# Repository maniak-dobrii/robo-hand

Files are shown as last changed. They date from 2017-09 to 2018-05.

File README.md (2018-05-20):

## I designed this robot to show finger to my friend

You will blame me for the size of that gif

Wi-Fi enabled robot that mimics human palm. Each finger is a set of rigid segments connected via revolute joints with rubber bands pulling them together. Each finger is flexed by servo, that is attached to it via fishing line (rubber bands extend it back). Servos are controlled by ESP8266 based board.

You'll need [SketchUp](https://www.sketchup.com/) to export frame models for printing, palm is available in both `.stl` and `.skp`. [Autodesk Eagle](https://www.autodesk.com/products/eagle/free-download) is required  to export mask for PCB. Both SketchUp and Eagle have free versions enough for export.

Currently there is basic Wi-Fi-based control and two physical buttons, one for finger gesture, one for sign of the horns. Device spawns Wi-Fi hot spot and HTTP server, that serves HTML and performs gestures on GET.

### Palm
Palm itself is based on [design by Juan Gutierrez](https://www.thingiverse.com/thing:14986). In original design I didn't like thumb placement. If you only need the palm, I have it on [thingiverse](https://www.thingiverse.com/thing:2743350).

Except, of course, a 3D printer and filament, for palm you'll need:
 - **fishing line** to attach fingers to servos, could be found in a supermarket or fishing equipment store, anything will go,
 - **21 x m3x12 screws and nuts** (4 for each finger, thumb needs 3, 2 for binding palm base halfs)
 - **at least 14 1/4” rubber bands**, you might need more depending on their strength (but don't worry they are cheap and sold in big enough amounts). You can get those in orthodontic shops, they are 1/4” in diameter. In Russian they are called "эластики" or "ортодонтические резинки" or "резиновые тяги", they also have names for different hardnesses, I got "Медведь" 1/4, 4,5oz (strong), "Сова" 1/4, 2oz (weak one).

For more details see my [thingiverse](https://www.thingiverse.com/thing:2743350) remix.

### Frame
Frame is 3D printed as well, I used honeycomb pattern to make it robust, require less filament and look cool. In order to print it you'll need at least **134x170mm printing area**. In order to reduce printing time, bottom frame panel that has servos and PCB mounts is separated into two parts that are secured together by screw joints. All joints require m3 screws (different length, 8-16) and nuts, there are 21 total case/frame screw joints. At some point of designing frame I suddenly got deadlines, that lead to some fast decisions, so I can't tell which m3 screw lengths I used, just get yourself a kit of all sizes from 8 to 16mm.

### PCB and electronics
PCB here is just to avoid confusing wiring making construction more modular and clear. PCB allows more convenient connection between servos, ESP8266 board, power supply and power switch. It appeared that after all this years I've lost almost all my expertise in building PCBs, so don't learn from me on that =) Also, I've messed every thing possible in Eagle project, but it works.

Main PCB has a socket for Wemos D1 mini board, soldered DC jack and lots of pinheads to connect servos and buttons module. Buttons module hold tact switches that provide physical control.

 - ESP8266 board is some Wemos D1 mini clone I got from [aliexpress](https://ru.aliexpress.com/item/D1-mini-V2-Mini-NodeMcu-4M-bytes-Lua-WIFI-Internet-of-Things-development-board-based-ESP8266/32681374223.html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), it has usb port and you can program it via Arduino IDE.
 - Power brick was excavated from my pile of "stuff to use somewhere", 5V 1A, that still works for 5x250ma servos peak draw and around 250ma peak ESP8266 draw (didn't test with wi-fi yet).
 - Power switch was the one that looked the best, mine was MRS-102A-C3, top frame panel has mounting hole for it.
 - Power jack is DS-201.
 - All servos are SG90. [SG90 SketchUp model](https://3dwarehouse.sketchup.com/model/b4d110b53afe39d821cd77f5063eab61/Servo-Tower-Pro-Micro-SG-90-with-horns) and was initially created by [James W.](https://3dwarehouse.sketchup.com/user/0712161666807539621944321/James-W?nav=models) and then updated by me according to real servos measurements.
 - Tact switches on buttons PCB are both 0350HIM-180G-G.
 
### Firmware
ESP8266 could be programmed via Arduino IDE, especially if you have development board like I do with usb hardware attached. You work with servos and inputs/outputs just like you do with Arduino. That means that your Arduino experience is relevant here and there are loads of info on the internet.

### Links to some parts
The way I approach such projects is that I often take breaks, really long breaks enough, for example, for my 3D printer to get covered with dust. So I tend to write everything down and I won't have to do research again. This time I was even not that lazy to keep a repo live. Here are parts I used, hope links won't be dead next time I look:
- Good quality cool black hex m3 screws and nuts set with a case, more enough to build this project: https://aliexpress.com/item/280Pcs-Set-M3-Cap-Head-Hex-Socket-Bolt-Screw-Nut-Metric-Machine-Fastener-Assortment-Set/32802252084.html
- Single size hex m3 screws, if you think you'll need more: https://www.aliexpress.com/item/New-24pcs-Lot-M3-Fully-Threaded-Black-Hex-Socket-Cap-Head-Screw-Bolt-Fastener-Set/32783442556.html
- m3 nuts, in case you want to stock up: https://www.aliexpress.com/item/100pcs-Metric-Thread-M3-M4-M5-M6-Black-Carbon-Steel-Hex-Nut-Hexagonal-Nut/32806225058.html
- Wemos D1 mini clone (ESP8266 board with usb): https://www.aliexpress.com/item/1PCS-D1-mini-Mini-NodeMcu-4M-bytes-Lua-WIFI-Internet-of-Things-development-board-based-ESP8266/32681374223.html
- SG90 servos - 10 pack: https://www.aliexpress.com/item/10PCS-9G-SG90-towerpro-micro-servo-motor-RC-Robot-Helicopter-Airplane-control/32326627136.html

All the other stuff I got from my local suppliers.

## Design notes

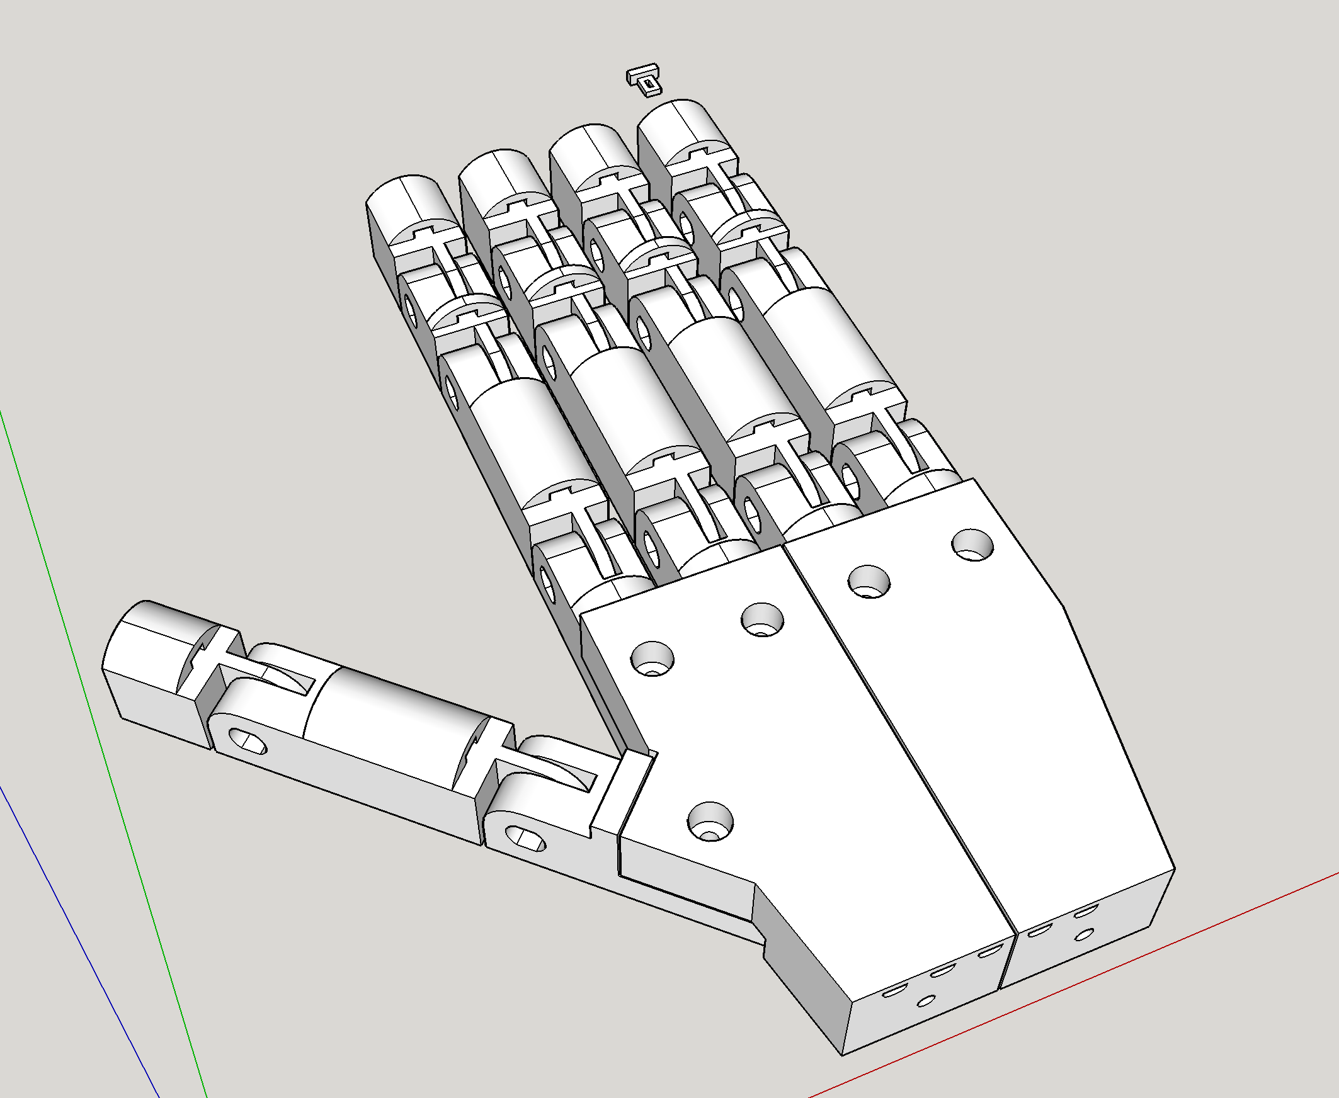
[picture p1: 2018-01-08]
images/palm.png

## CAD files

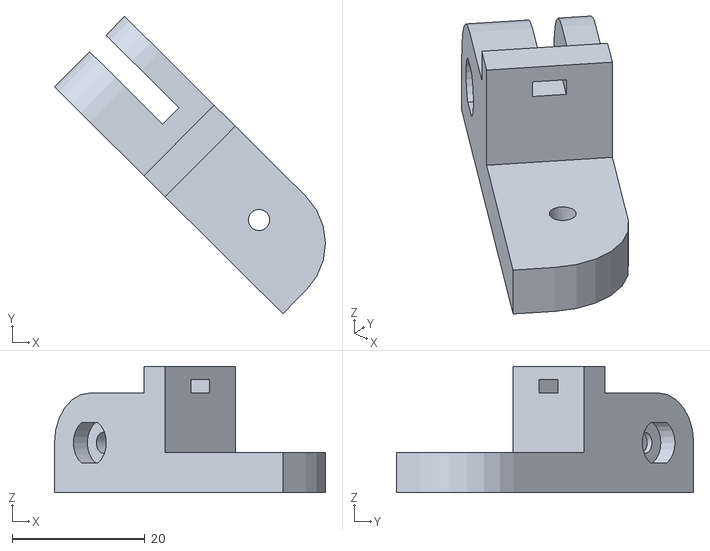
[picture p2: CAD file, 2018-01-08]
3D models/palm_stl/thumb_base.stl
40.8 x 44.8 x 19.0

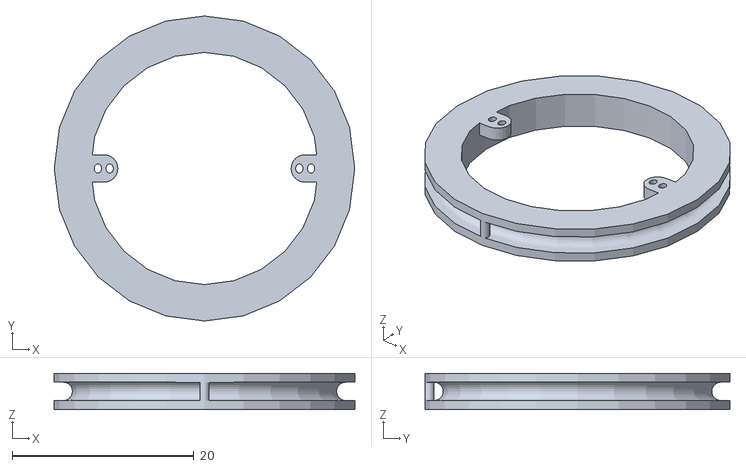
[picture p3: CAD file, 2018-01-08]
3D models/stl/driver45mm.stl
33.0 x 33.5 x 4.00

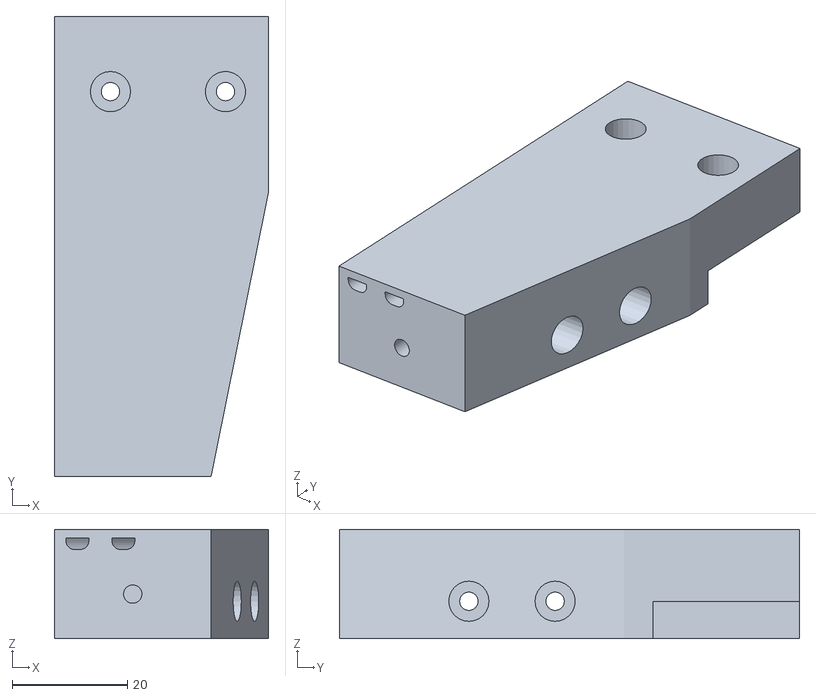
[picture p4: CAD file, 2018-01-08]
3D models/palm_stl/half_palm.stl
37.3 x 80.0 x 19.0

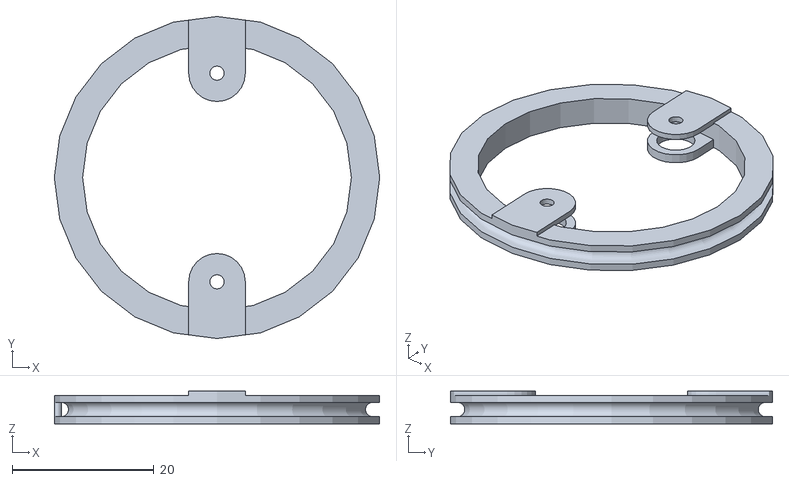
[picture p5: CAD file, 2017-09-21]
3D models/stl/driver.stl
45.9 x 45.4 x 4.60

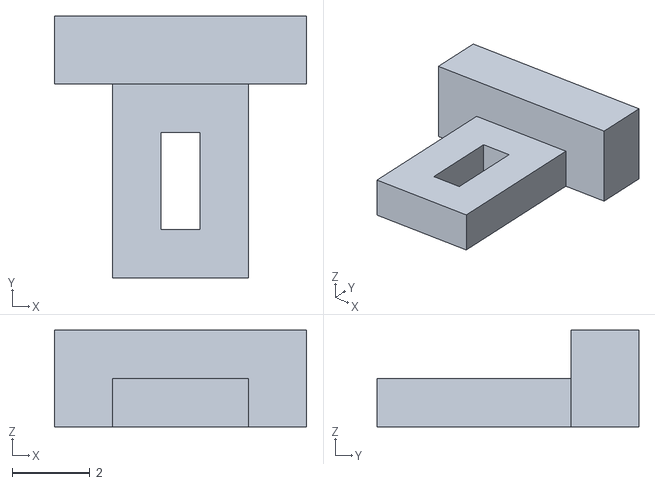
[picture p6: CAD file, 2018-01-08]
3D models/palm_stl/string_finger_tip_terminal.stl
6.50 x 6.75 x 2.50

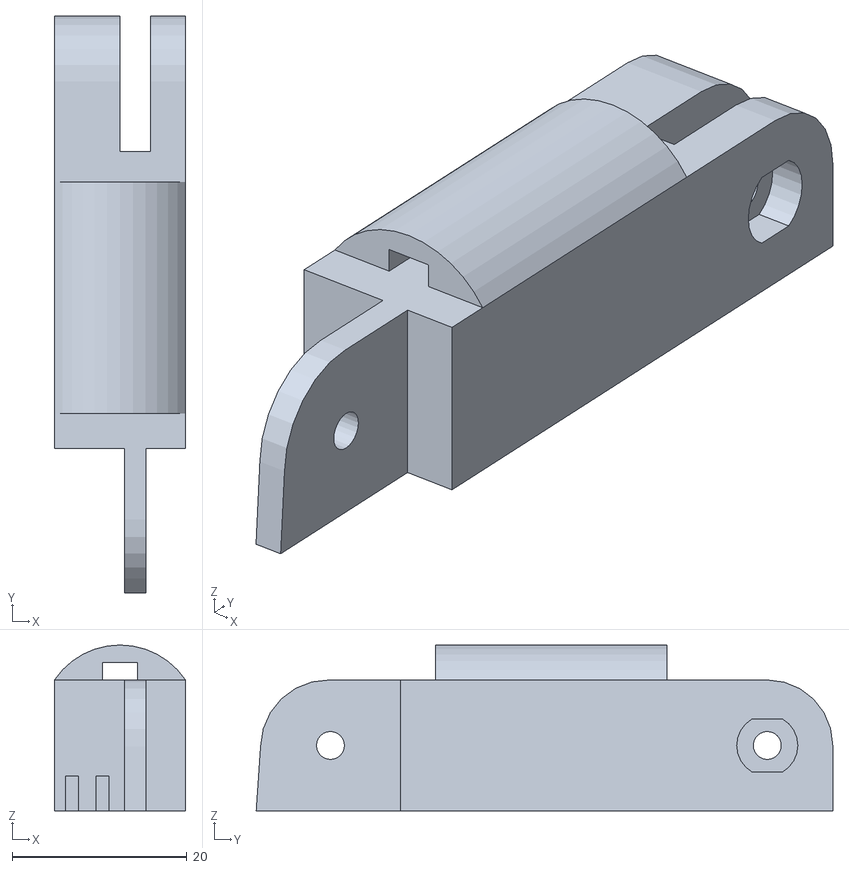
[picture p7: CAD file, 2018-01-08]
3D models/palm_stl/finger_section_1.stl
15.0 x 66.0 x 19.0

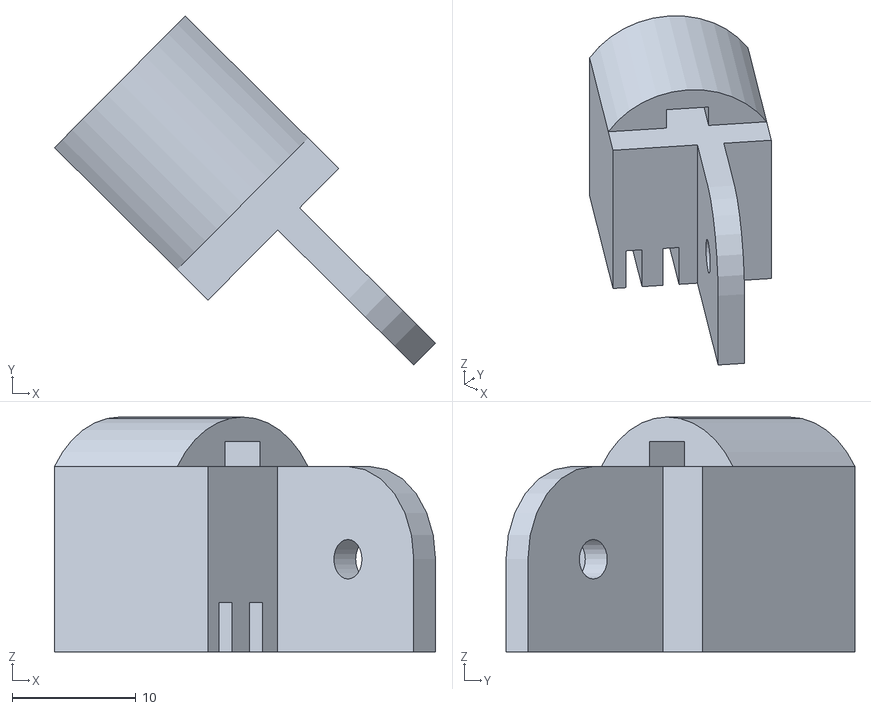
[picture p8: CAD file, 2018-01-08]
3D models/palm_stl/thumb_tip.stl
30.8 x 28.2 x 19.0

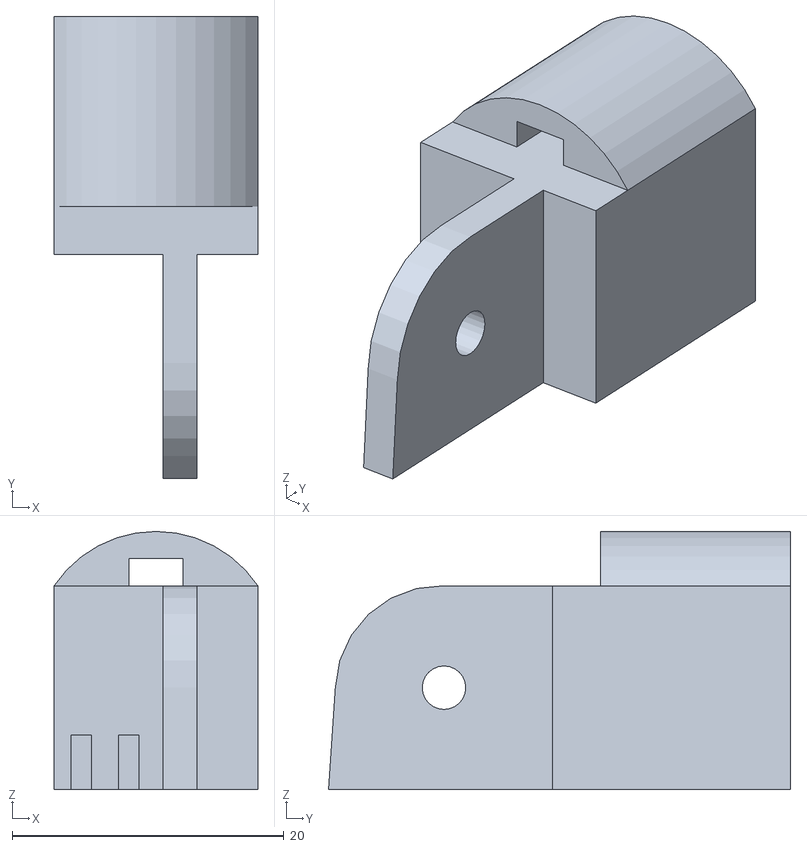
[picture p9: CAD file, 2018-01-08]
3D models/palm_stl/finger_tip.stl
15.0 x 34.0 x 19.0

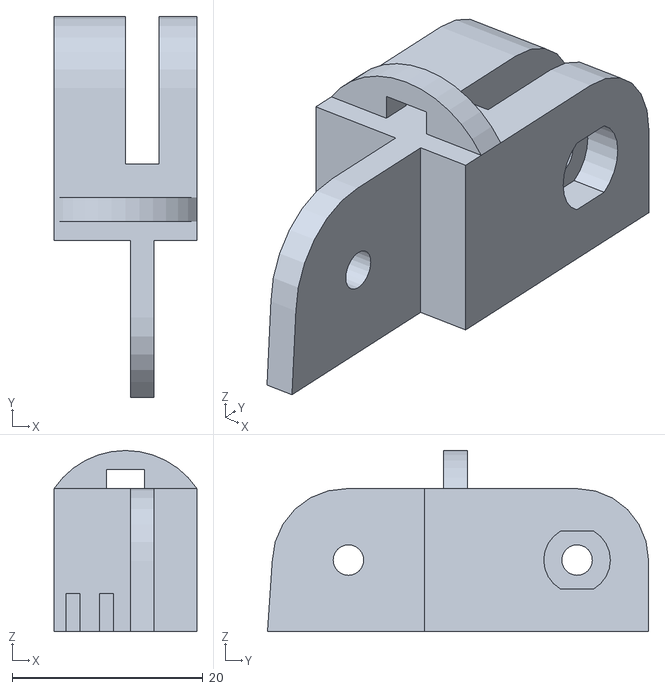
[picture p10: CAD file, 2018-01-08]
3D models/palm_stl/finger_section_2.stl
15.0 x 40.0 x 19.0

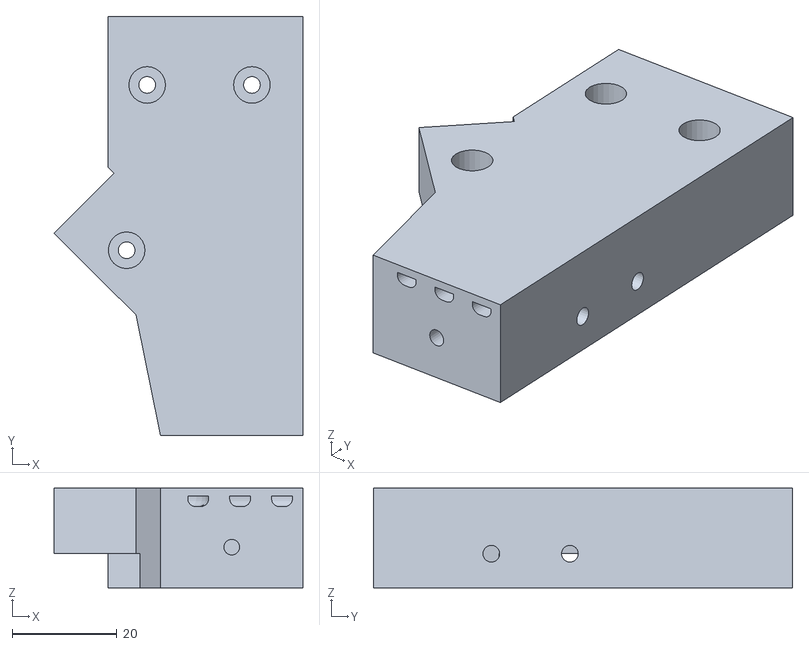
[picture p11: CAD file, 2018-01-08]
3D models/palm_stl/half_palm_w_thumb.stl
47.5 x 80.0 x 19.0

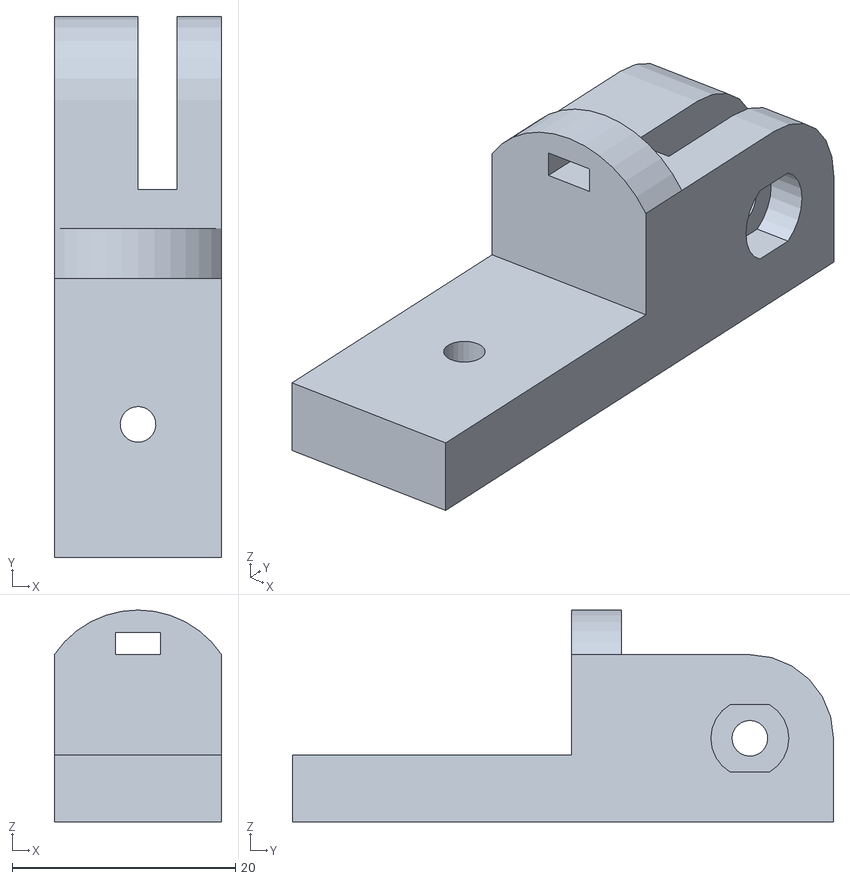
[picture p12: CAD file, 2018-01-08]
3D models/palm_stl/finger_base.stl
15.0 x 48.5 x 19.0

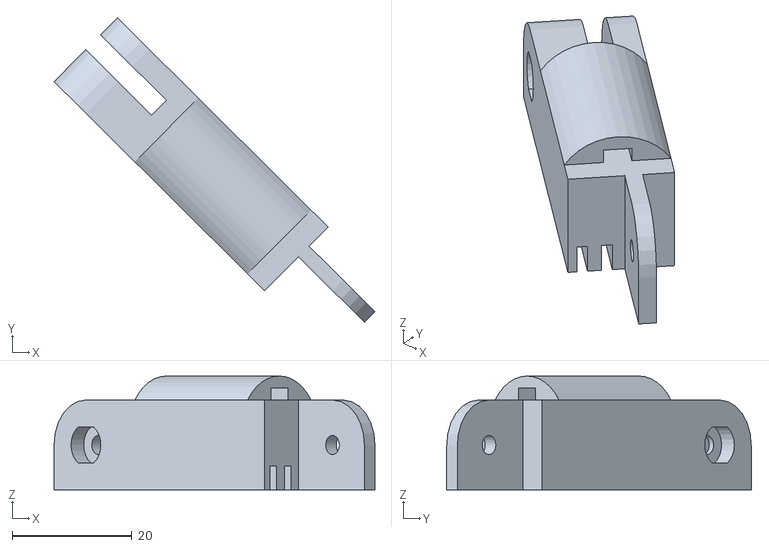
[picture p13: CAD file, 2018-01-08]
3D models/palm_stl/thumb_section_1.stl
53.5 x 50.8 x 19.0

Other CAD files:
3D models/button_icons.skp
3D models/honeycomb_pattern.skp
3D models/nut_hole.skp
3D models/palm.skp
robo_hand.skp

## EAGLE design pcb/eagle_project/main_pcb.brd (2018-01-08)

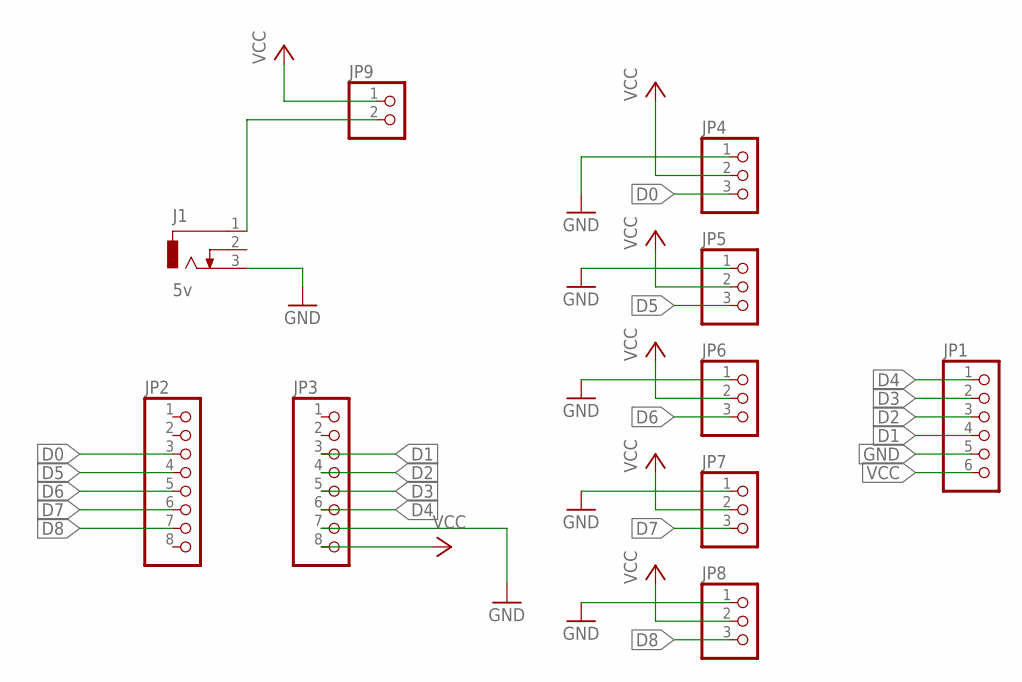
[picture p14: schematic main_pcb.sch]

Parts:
J1: 5v; DCJ0303
JP1: PINHD-1X6; 1X06
JP2, JP3: PINHD-1X8; 1X08
JP4, JP5, JP6, JP7, JP8: PINHD-1X3; 1X03
JP9: PINHD-1X2; 1X02

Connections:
D0: JP2.3, JP4.3
D1: JP1.4, JP3.3
D2: JP1.3, JP3.4
D3: JP1.2, JP3.5
D4: JP1.1, JP3.6
D5: JP2.4, JP5.3
D6: JP2.5, JP6.3
D7: JP2.6, JP7.3
D8: JP2.7, JP8.3
GND: J1.3, JP1.5, JP3.7, JP4.1, JP5.1, JP6.1, JP7.1, JP8.1
unnamed: J1.1, JP9.2
VCC: JP1.6, JP3.8, JP4.2, JP5.2, JP6.2, JP7.2, JP8.2, JP9.1

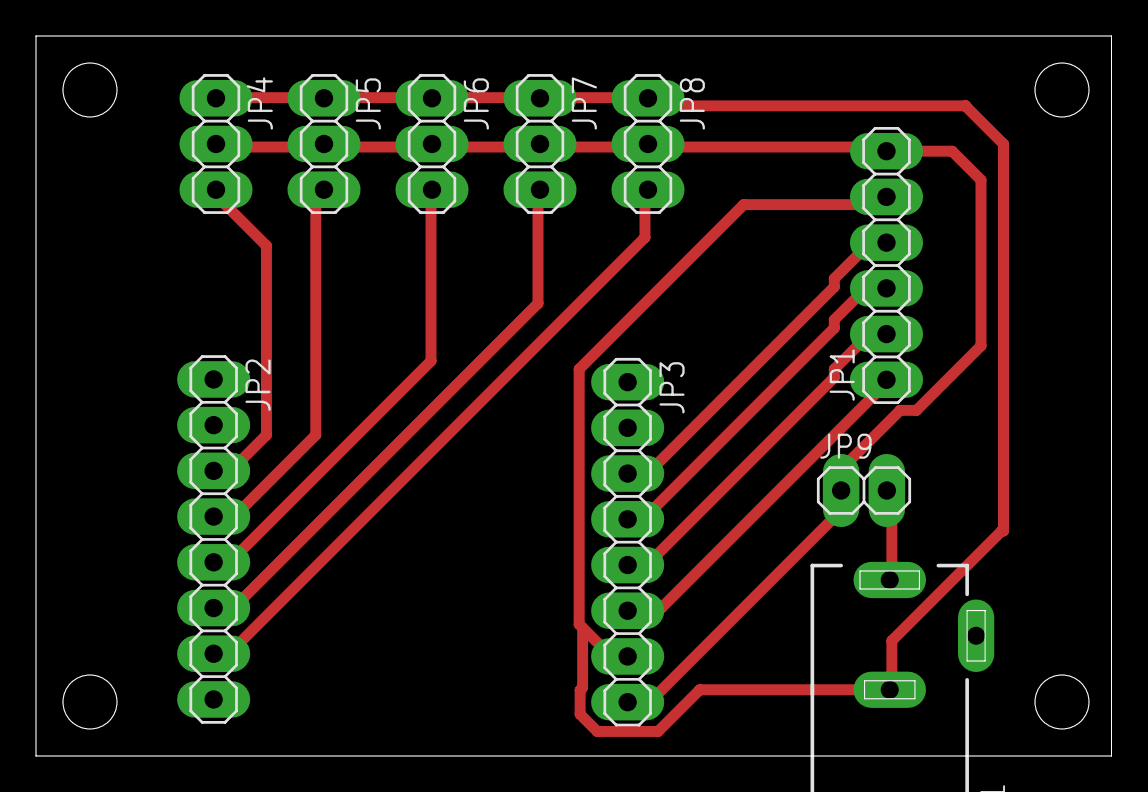
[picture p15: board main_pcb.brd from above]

Board: 1 copper layer, 59.8 x 40.0 mm, 10 parts (0 on the bottom side), 12 nets.

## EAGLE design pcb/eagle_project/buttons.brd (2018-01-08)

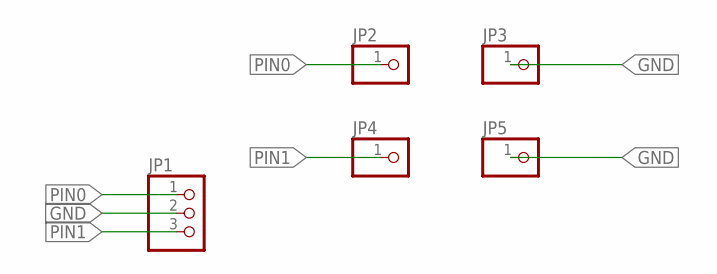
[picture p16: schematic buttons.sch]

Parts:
JP1: PINHD-1X3; 1X03
JP2, JP3, JP4, JP5: PINHD-1X1; 1X01

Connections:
GND: JP1.2, JP3.1, JP5.1
PIN0: JP1.1, JP2.1
PIN1: JP1.3, JP4.1

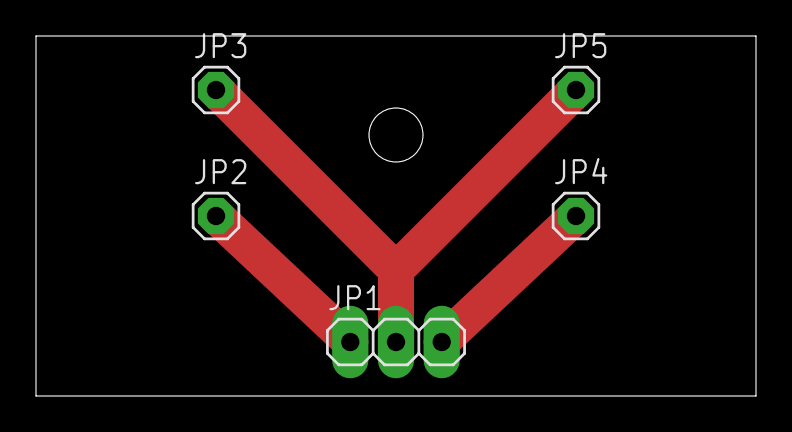
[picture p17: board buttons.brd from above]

Board: 1 copper layer, 40.0 x 20.0 mm, 5 parts (0 on the bottom side), 3 nets.

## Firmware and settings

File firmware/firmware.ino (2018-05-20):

/*
 * MANIAK_dobrii's Robo hand firmware.
 * 
 * Currently you need to connect to Wi-Fi hotspot, html-based control is available on 192.168.4.1, will switch to (maybe) JSON API later.
 * Hardware buttons control is as well available, you can press/release, press/hold/release.
 */

#include "CommandDispatcher/command_loop.h"
#include "CommandDispatcher/function_command.h"
#include "PalmHardware.h"

#include <ESP8266WiFi.h>
#include <WiFiClient.h> 
#include <ESP8266WebServer.h>


CommandDispatcher commandDispatcher(64); // 64 - max number of waiting commands
PalmHardware palm;

// Wi-Fi hotspot configuration
const char *ssid = "robo-hand";
const char *password = "robo-hand";

ESP8266WebServer server(80);


//
// Basic palm operations
//
void koza();
void fuck();
void fullOpen();

//
// ServerCommands
//
void sendControlPage();
void handleRoot();
void handleKoza();
void handleFuck();
void handleGesture();



void setup() {
  palm.setup();
  palm.setButtonsCallback(onButtonsEvent);

  setupWiFiAndServer();
}

void setupWiFiAndServer() {
  delay(1000);
  Serial.begin(115200);
  Serial.println();
  Serial.print("Configuring access point...");
  /* You can remove the password parameter if you want the AP to be open. */
  WiFi.softAP(ssid, password);

  IPAddress myIP = WiFi.softAPIP();
  Serial.print("AP IP address: ");
  Serial.println(myIP);
  server.on("/", handleRoot);
  server.on("/koza", handleKoza);
  server.on("/fuck", handleFuck);
  server.on("/gesture", handleGesture);
  server.begin();
  Serial.println("HTTP server started");  
}

void loop() 
{
  commandDispatcher.dispatch(millis());
  palm.updateButtons();
  server.handleClient();
} 


//
// Button events processing
//
Milliseconds lastPerformTimestamp = 0;
Milliseconds gesturePerformThresold = 1000;

void onButtonsEvent(kRHButton button, kRHButtonEvent event) {
  /*
   * I wanted better UX when you can have two things:
   *  1. Fast button press => palm perfoms gesture and expands back
   *  2. Press and hold => palm holds gesture and keeps it until you release the button
   *  
   *  That's why here on button Up fullOpen is immediately scheduled, while
   *  on button Down gesture is only scheduled if time thresold passed.
   */
  
  Milliseconds timeFromLastPerform = millis() - lastPerformTimestamp;
  
  if(event == kRHButtonEventUp) {
    Milliseconds afterDelay = (timeFromLastPerform > 500) ? 0 : 500;
    commandDispatcher.push(afterDelay, new FunctionCommand(fullOpen));
  } else {
    if(timeFromLastPerform > gesturePerformThresold) {
      Command *command = nullptr;

      switch(button) {
        case kRHButtonKoza: {
          command = new FunctionCommand(koza);
          break;
        }

        case kRHButtonFuck: {
          command = new FunctionCommand(fuck);
          break;
        }
      }

      commandDispatcher.push(0, command);
      lastPerformTimestamp = millis();
    }
  }
}


//
// Functions that could be passed into FunctionCommand.
//
void koza() {
  palm.koza();
}

void fuck() {
  palm.fuck();
}

void fullOpen() {
  palm.fullOpen();
}


//
// Server called functions
//
void sendControlPage() {
  server.send(200, "text/html", "<a href=\"koza\">koza</a>  |  <a href=\"fuck\">fuck</a>");  
}

void handleRoot() {
  sendControlPage();
}

void handleKoza() {
  commandDispatcher.push(0, new FunctionCommand(koza));
  commandDispatcher.push(500, new FunctionCommand(fullOpen));
  
  sendControlPage();
}

void handleFuck() {
  commandDispatcher.push(0, new FunctionCommand(fuck));
  commandDispatcher.push(500, new FunctionCommand(fullOpen));
  
  sendControlPage();
}

void handleGesture() {
  // this needs work, so it is not implemented yet
  
//  String value = server.arg("thumb");
//  if(value.length() > 0) {
//    palm.extendFinger(kRHFingerThumb, value.toFloat());
//  }

  sendControlPage();
}

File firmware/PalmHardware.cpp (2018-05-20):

// MANIAK_dobrii's Robo hand firmware prototype

#include "PalmHardware.h"
#include <Servo.h>

// Some servos are mounted in a way that clockwise rotation pulls the string, others
// are vice versa. This is used during servos binding in setup, 
// depends on how everything is connected in hardware.
enum kRHBindingDirection {
  kRHBindingDirectionLeft,
  kRHBindingDirectionRight
};

// Min and max angles for fingers in degrees
const int kRHAngleOpen = 170; // should be greater than kRHAngleClosed
const int kRHAngleClosed = 0; // should be less than kRHAngleOpen

const int servoCount = 5; // 5 fingers, right?
Servo servo[servoCount]; // servos to be attached
kRHBindingDirection bindings[servoCount]; // binding direction for each servo, see description above

const uint8_t kKozaButtonPin = D1;
const uint8_t kFuckButtonPin = D2;

PalmHardware::PalmHardware() {
  this->buttonsCallback = nullptr;
  this->buttonsListener = new ButtonListener(this);
}

void PalmHardware::setup() {
  //
  // servos
  servo[0].attach(D0);
  bindings[0] = kRHBindingDirectionLeft;
  
  servo[1].attach(D5);
  bindings[1] = kRHBindingDirectionRight;
  
  servo[2].attach(D6);
  bindings[2] = kRHBindingDirectionRight;
  
  servo[3].attach(D7);
  bindings[3] = kRHBindingDirectionRight;
  
  servo[4].attach(D8);
  bindings[4] = kRHBindingDirectionLeft;

  //
  // buttons
  pinMode(kKozaButtonPin, INPUT_PULLUP);
  pinMode(kFuckButtonPin, INPUT_PULLUP);
  this->buttonsListener->listenButtonOnPin(kKozaButtonPin);
  this->buttonsListener->listenButtonOnPin(kFuckButtonPin);

  //
  // Extend all fingers on start, that helps to avoid bugs
  // and serves as a feedback that hand started. I was thinking to extend that feedback, so
  // that hand won't have any other way to provide feedback rather then constantly move a little bit.
  this->fullOpen();
}

PalmHardware::~PalmHardware() {
  delete this->buttonsListener;
  this->buttonsListener = nullptr;
  
  for(int i=0; i<servoCount; i++) {
    servo[i].detach();
  }
}


void PalmHardware::updateButtons() {
  this->buttonsListener->update();
}

void PalmHardware::setButtonsCallback(RHButtonsCallback callback) {
  this->buttonsCallback = callback;
}

void PalmHardware::onButtonListenerEvent(ButtonListener *buttonListener, kButtonListenerEvent event, uint8_t pin) {

  kRHButtonEvent callbackEvent;
  kRHButton callbackButton;

  if(this->buttonEventForButtonListenerEvent(event, &callbackEvent) &&
    this->buttonForPin(pin, &callbackButton)) {
      notifyButtonEvent(callbackButton, callbackEvent);
  }
}

bool PalmHardware::buttonEventForButtonListenerEvent(kButtonListenerEvent event, kRHButtonEvent *output) {
  kRHButtonEvent outputEvent;
  
  switch(event) {
    case kButtonListenerEventButtonDown: {
      outputEvent = kRHButtonEventDown;
      break;
    }
    
    case kButtonListenerEventButtonUp: {
      outputEvent = kRHButtonEventUp;
      break;
    }

    default: {
      return false;
    }
  }

  if(output != nullptr) {
    *output = outputEvent;
  }

  return true;
}

bool PalmHardware::buttonForPin(uint8_t pin, kRHButton *output) {
  kRHButton outputButton;
  
  if(pin == kKozaButtonPin) {
    outputButton = kRHButtonKoza;
  } else if(pin == kFuckButtonPin) {
    outputButton = kRHButtonFuck;
  } else {
    return false;
  }

  if(output != nullptr) {
    *output = outputButton;
  }
  return true;
}

void PalmHardware::notifyButtonEvent(kRHButton button, kRHButtonEvent event) {
  if(this->buttonsCallback != nullptr) {
    this->buttonsCallback(button, event);
  }
}

///////////////////////////
// Helpers
///////////////////////////
void PalmHardware::writeAngleToServo(int servoPosition, int angle)
{
  if(servoPosition < 0) return;
  if(servoPosition >= servoCount) return;

  if(bindings[servoPosition] == kRHBindingDirectionRight)
  {
    angle = 180 - angle;
  }
  
  angle = this->limitAngle(angle);

  servo[servoPosition].write(angle);
}

int PalmHardware::limitAngle(int angle)
{
  if(angle > kRHAngleOpen) return kRHAngleOpen;
  if(angle < kRHAngleClosed) return kRHAngleClosed;

  return angle;
}

int PalmHardware::angleFromNormalized(float normalizedExtendRatio) {
  if(normalizedExtendRatio > 1.0) normalizedExtendRatio = 1.0;
  if(normalizedExtendRatio < 0.0) normalizedExtendRatio = 0.0;

  return kRHAngleClosed + ((double)(kRHAngleOpen - kRHAngleClosed)) * normalizedExtendRatio;
}

void PalmHardware::extendFinger(kRHFinger finger, float normalizedExtendRatio) {
  this->writeAngleToServo(finger, angleFromNormalized(normalizedExtendRatio));
}


///////////////////////////
// Gesture Presets
///////////////////////////
void PalmHardware::fuck() {
  this->writeAngleToServo(kRHFingerMiddle, kRHAngleOpen);

  this->writeAngleToServo(kRHFingerThumb, kRHAngleClosed);
  this->writeAngleToServo(kRHFingerIndex, kRHAngleClosed);
  this->writeAngleToServo(kRHFingerRingFinder, kRHAngleClosed);
  this->writeAngleToServo(kRHFingerPinky, kRHAngleClosed);
}
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

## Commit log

2017-09-17 Initial messy loadup
    [finger_base.stl, finger_section_1.stl, finger_section_2.stl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]
2017-09-17 Removed all generatable files except finger gcode
    [finger_base.stl, finger_section_1.stl, finger_section_2.stl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]
2017-09-17 Cleaned main skp file
    [robo_hand.skp]
2017-09-17 Added SG90 servo with field + readme mentions
    [robo_hand.skp]
2017-09-17 Servos with new bindings first arrangement
    [robo_hand.skp]
2017-09-17 Added new driver idea (raw incorrect size)
    [robo_hand.skp]
2017-09-20 Added driver profile
    [robo_hand.skp]
2017-09-20 Added driver ring
    [robo_hand.skp]
2017-09-20 Added bindings (not yet added to the driver ring)
    [robo_hand.skp]
2017-09-20 Joined bindings to the driver ring
    [robo_hand.skp]
2017-09-21 Added first driver version stl, gcode
    [driver.stl, robo_hand.skp]
2017-09-21 Added 45mm driver ring
    [robo_hand.skp]
2017-09-21 Added 45mm driver
    [robo_hand.skp]
2017-09-21 Rotaded servos taking into account wires position
    [robo_hand.skp]
2017-10-30 Updated driver relative x/y positions
    [robo_hand.skp]
2017-10-30 Refined servo sizes
    [robo_hand.skp]
2017-10-30 First servo holders (without additional 'corners' for better stability)
    [robo_hand.skp]
2017-10-31 Unmerged first try driver holder
    [robo_hand.skp]
2017-10-31 Jined servo holder, with tight holes
    [robo_hand.skp]
2017-11-05 Increased servo holder hole diameter to 1.6mm
    [robo_hand.skp]
2017-11-05 Removed bazilion redundunt guides
    [robo_hand.skp]
2017-11-05 Added servo holders to servo components
    [robo_hand.skp]
2017-11-05 Arranged servos and angle changers
    [robo_hand.skp]
2017-11-06 Updated box sizes, added honeycomb grid surface
    [robo_hand.skp]
2017-11-06 Updated box dimensions, added honeycomb pattern as separate file
    [honeycomb_pattern.skp]
2017-11-12 Sized case base
2017-11-12 Sized case base to 164x134mm
2017-11-12 Formed case bottom plate without holes and joined servo holders
2017-11-12 Added case bottom plate copy to the scene
2017-11-12 Decided to keep walls 6mm(3mm separator, 3mm bolt hole), extruded front panel without holes and top notches
2017-11-12 Added front to bottom panel mounting holes
2017-11-12 Added bevel to bottom plate
2017-11-19 Extended base length to 170mm, added temporary back panel, positioned pcb
2017-11-19 Added pcb stands
2017-11-25 Separating bottom plate: added first cut (holes not cut)
2017-11-25 Fixed bottom plate holes
2017-11-25 Added one more cut to the bottom plate
2017-11-25 Separated bottom plate into two parts (without holes)
2017-11-25 Added strings holder hole mounts to the front panel
2017-11-25 Added side panel frames (without holes)
2017-11-25 Removed internal wall from the back panel, frame first, details later
2017-11-25 Created intercomponent holes in the bottom panel
2017-11-26 Added side holes to the front and side panels
2017-11-26 Added holes for bottom plate fishing line joints
2017-12-03 Not sure what, but used to print second part of the bottom panel
2017-12-17 New top buttons module, redesigned back, top and right panel (including holes, honeycomb pattern and switch socket)
2017-12-24 Fixed buttons model (left button got clamped during gcode generation)
2017-12-24 Added simplified hands with gestures for button icons
2017-12-24 Button pictures before subtraction
2017-12-24 (fixed bottoms) Button pictures before subtraction
2018-01-02 Added separate palm .skp
    [palm.skp]
2018-01-08 Removed all redundant stuff, added missing binding holes (front panel to top panel) that I forgot to add previously
2018-01-08 Fixed palm absolute position
    [palm.skp]
2018-01-08 Moved nut hole to separate file
    [nut_hole.skp]
2018-01-08 Moved button icons to separate file
    [button_icons.skp]
2018-01-08 Removed redundant files
    [driver45mm.stl, finger_base.stl, finger_section_1.stl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]
2018-01-08 Moved 3D models to separate directory
    [button_icons.skp, driver.stl, driver45mm.stl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]
2018-01-08 Added pretty shamefull pcb design, hope nobody sees it, wait, I'm putting it on the internet, ook
    [DRILEGEND.CFG, buttons.brd, buttons.sch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]
2018-01-08 Added prototype firmware (buttons only, no wifi)
2018-05-20 Refactored button listening routine into separate class, PalmHardware now listens to button events via ButtonListener and translates them to the outer world. New button-control UX, fast press to show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
2018-05-20 Hooked over-Wi-Fi control along with hardware buttons control
